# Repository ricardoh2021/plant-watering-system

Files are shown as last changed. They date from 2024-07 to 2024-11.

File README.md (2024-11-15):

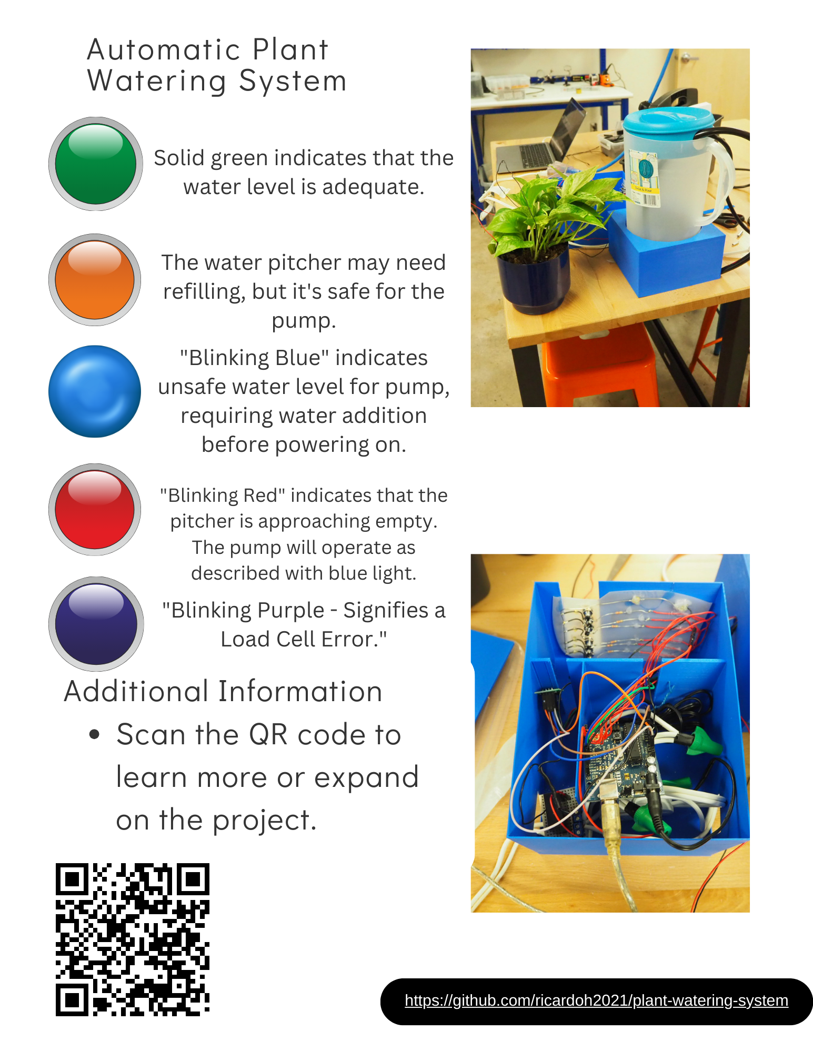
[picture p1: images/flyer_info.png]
System Flyer


# Water 1.1

**Author:** Ricardo Hernandez

## Table of Contents

1. [Description](#description)
2. [Changelog](#changelog)
3. [IDE Setup Instructions](#ide-setup-instructions)
4. [Advice for Beginners](#advice-for-beginners)
5. [Plant Watering System Documentation](#plant-watering-system-documentation)
   - [Overview](#overview)
   - [Components](#components)
   - [Pin Definitions](#pin-definitions)
   - [Arduino Wiring Schematic](#arduino-wiring-schematic)
   - [Configuration](#configuration)
   - [Functional Description](#functional-description)
     - [LED Indicators](#led-indicators)
     - [LED Blinks](#led-blinks)
     - [Error Handling](#error-handling)
   - [Functions](#functions)
     - [`setColor(int R, int G, int B)`](#setcolorint-r-int-g-int-b)
     - [`blinkLed(int R, int G, int B, unsigned long duration, unsigned long blinkInterval)`](#blinkledint-r-int-g-int-b-unsigned-long-duration-unsigned-long-blinkinterval)
     - [`blinkPurple()`](#blinkpurple)
     - [`blinkRed()`](#blinkred)
     - [`blinkBlue()`](#blinkblue)
     - [`resetLeds()`](#resetleds)
     - [`insertionSort(int* arr, int n)`](#insertionsortint-arr-int-n)
     - [`performMoistureReadings()`](#performmoisturereadings)
     - [`updateMoistureStatus()`](#updatemoisturestatus)
     - [`checkMoisture()`](#checkmoisture)
     - [`waterPlant()`](#waterplant)
     - [`checkLoadCellError(float weight)`](#checkloadcellerrorfloat-weight)
   - [Initialization](#initialization)
   - [Main Loop](#main-loop)
   - [3D Printed Encasings](#3d-printed-encasings)
     - [Encasing for Scale and Pitcher](#encasing-for-scale-and-pitcher)
     - [Encasing for Arduino and Wires](#encasing-for-arduino-and-wires)
   - [Design Process in TinkerCAD](#design-process-in-tinkercad)
   - [Printing with Innovation Creativity Lab](#printing-with-innovation-creativity-lab)
   - [3D Printed Model Files](#3d-printed-model-files)
   - [Known Issues and Troubleshooting](#known-issues-and-troubleshooting)
   - [Failsafe Values](#failsafe-values)
6. [General Tips](#general-tips)
7. [Future Modifications](#future-modifications)
8. [Upgrade Considerations](#upgrade-considerations)
   - [Hardware Upgrade Suggestions](#hardware-upgrade-suggestions)
   - [Possible Modifications for Indoor Plant Watering System](#possible-modifications-for-indoor-plant-watering-system)
9. [Nail Placement](#nail-placement)
10. [General TroubleSHooting](#general-troubleshooting)

## Description

Water 1.0 is an automated plant watering system that uses sensors to measure soil moisture and controls a pump via a relay to water the plant when needed. This project is inspired by the Botanicalls and Growduino concepts.

For information about the original project started by Leo Marte `09, visit: [Water 1.0 Project](http://cs.gettysburg.edu/~tneller/cs450/08fa/Physical_Computing/Plant_Watering.html)

## Changelog

- **2024-07-22:** (Ricardo Hernandez) Optimized and refactored code for better readability and performance. Updated comments.
- **2024-08-31:** (Ricardo Hernandez) Integrated Load Cell Scale, RGB LED, into the watering system.

## IDE Setup Instructions

(as of July 23, 2024 using v2.3.2)

1. Ensure you have the latest version of the Arduino IDE installed.
2. Select the correct board and port:
   - **Board:** Arduino Duemilanove or Diecimila
   - **Port:** Select the appropriate COM port
     - On Windows: Select the appropriate COM port (e.g., COM3, COM4, etc.)
     - On macOS: Select the appropriate port (e.g., /dev/tty.usbmodemxxxxx or /dev/cu.usbserial-xxxxx)
3. Select the correct processor:
   - **Processor:** ATmega168 (Due to the age of the Arduino)
4. Compile and upload the code to the Arduino board.

## Advice for Beginners

If you’re new to this and feeling overwhelmed, my advice is simple: just go for it! Don't be afraid to dive in and learn something new along the way. There are countless YouTube videos and tutorials on Arduino projects that can guide you. Break the problem down into smaller pieces and build from there. Start experimenting—it's the best way to learn.

This project is meant for you to expand on! Take advantage of all the tools Gettysburg College offers, like the Innovation and Creativity Lab. Don’t hesitate to ask whoever is in charge of the lab for help. Professor Neller is also a fantastic resource, so don’t be intimidated by all the wiring (my fault, haha) or if it seems complicated at first. Looks can be deceiving, but you can always start with a personal Arduino kit to get familiar with how things work. Take baby steps, and you’ll find yourself understanding more and more as you go. Enjoy your time at Gettysburg College and feel free to clone this branch and expand on it!

TL;DR

- Just dive in—learning by doing is the best approach.
- Use YouTube and tutorials to guide you through Arduino projects.
- Break the problem into smaller pieces and build from there.
- Leverage Gettysburg College’s Innovation and Creativity Lab.
- Don’t hesitate to ask for help; Professor Neller is a great resource.
- Start with a personal Arduino kit to get familiar with the basics.

Have fun!

## Plant Watering System Documentation

### Overview

This documentation describes the functionality and configuration of a plant watering system. The system uses a load cell to measure the weight of the water pitcher, moisture sensors to determine soil moisture, and an RGB LED for feedback. It also includes failsafe conditions to handle errors and abnormal situations.

### Components

- **Load Cell**: Measures the weight of the water pitcher.
- **HX711**: Amplifies and converts the load cell signal.
- **Moisture Sensors**: Measures soil moisture levels.
- **RGB LED**: Provides visual feedback about the system status.
- **Relay**: Controls the water pump.
- **EEPROM**: Stores the zero factor for the load cell.
- **Arduino**: Arduino Diecimila

### Pin Definitions

- **Load Cell DOUT Pin**: `A4`
- **Load Cell SCK Pin**: `A5`
- **Red LED Pin**: `10`
- **Green LED Pin**: `11`
- **Blue LED Pin**: `12`
- **Relay Pin**: `9`
- **Power Pin**: `8`
- **Moisture Probe Pin**: `0`
- **Status LEDs**: Pins `2-7`

### Arduino Wiring Schematic

Below is the wiring schematic for the plant watering system using Arduino.

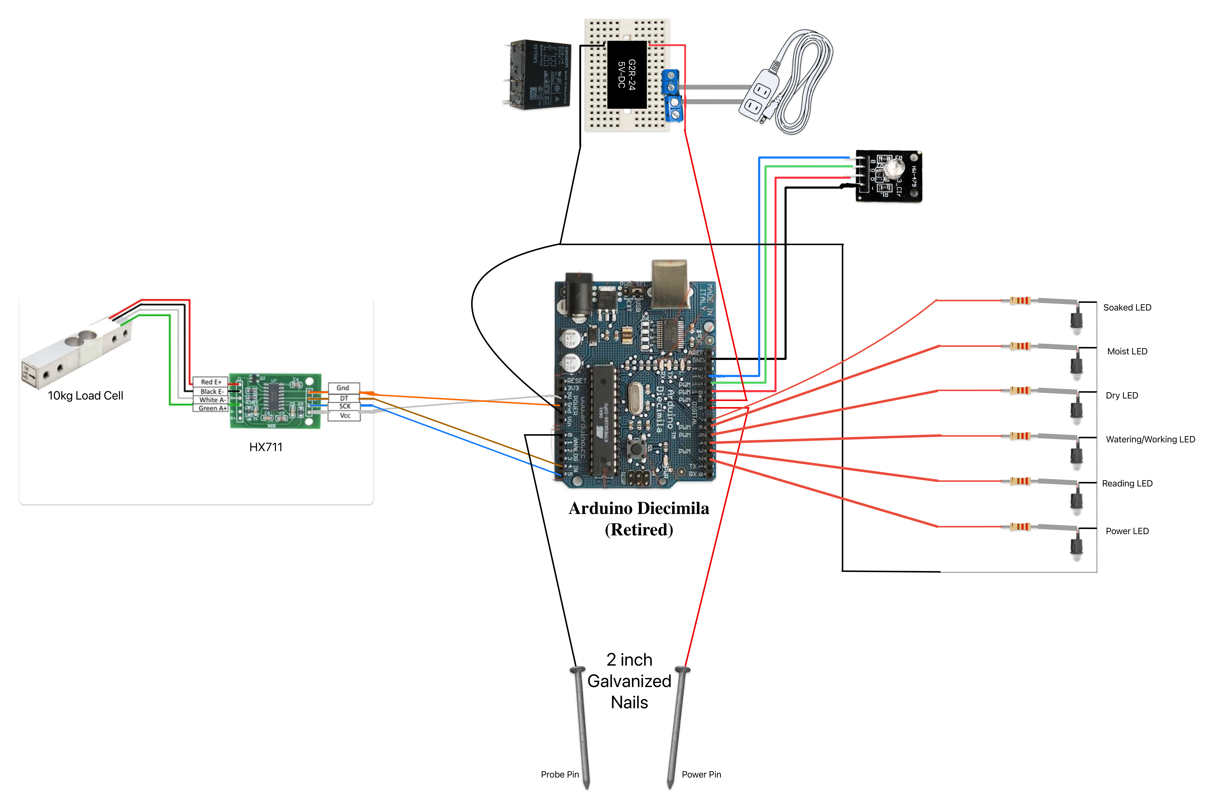
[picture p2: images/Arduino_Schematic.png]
Arduino Wiring Schematic


### Configuration

- **RGB LED Brightness Level**: `0.5`
- **Calibration Factor**: `-94500`
- **Weight Thresholds**:
  - **Empty Weight Threshold**: `1.65 lbs`
  - **Low Weight Threshold**: `3.00 lbs`
  - **Sufficient Weight Threshold**: `4.00 lbs`
- **Moisture Levels**:
  - **Dry**: `420`
  - **Moist**: `710`
  - **Soaked**: `1000`
- **Intervals**:
  - **Moisture Check Interval**: `10000 ms`
  - **Moisture Sample Interval**: `2000 ms`
  - **Water Interval**: `3000 ms`
  - **Failsafe Value**: `200`

### Functional Description

#### LED Indicators

- **Dry LED (Pin 5)**: Indicates that the soil is very dry.
- **Moist LED (Pin 6)**: Indicates that the soil is moist.
- **Soaked LED (Pin 7)**: Indicates that the soil is soaked.

#### LED Blinks

- **Purple Blink**: Indicates a load cell error.
- **Red Blink**: Indicates that the water level is too low.
- **Blue Blink**: Indicates a low water level warning.

#### Error Handling

- **Load Cell Error**: Detected if weight readings are outside a plausible range. The system blinks purple and sets `pumpEnabled` to `true`.
- **Low Water Level**: Detected if weight is below `EMPTY_WEIGHT_THRESHOLD` or `LOW_WEIGHT_THRESHOLD`. The system blinks red or blue, respectively, and sets `lowWaterLevel` to `true`.

### Functions

#### `setColor(int R, int G, int B)`

Sets the color of the RGB LED by adjusting the brightness of the red, green, and blue components.

#### `blinkLed(int R, int G, int B, unsigned long duration, unsigned long blinkInterval)`

Blinks the RGB LED with the specified color, duration, and interval.

#### `blinkPurple()`

Blinks the LED purple to indicate an error.

#### `blinkRed()`

Blinks the LED red to indicate a low water level.

#### `blinkBlue()`

Blinks the LED blue to indicate a low water level warning.

#### `resetLeds()`

Turns off all moisture status LEDs.

#### `insertionSort(int* arr, int n)`

Sorts an array of integers using insertion sort.

#### `performMoistureReadings()`

Averages moisture sensor readings over a defined interval and updates the average moisture level.

#### `updateMoistureStatus()`

Updates the status LEDs and triggers watering based on the average moisture level.

#### `checkMoisture()`

Determines if the plant needs watering based on moisture sensor readings.

#### `waterPlant()`

Controls the relay to water the plant if conditions are met.

#### `checkLoadCellError(float weight)`

Checks for errors in load cell readings and adjusts the system state accordingly.

### Initialization

The initialization routine sets up pin modes, initial states, and EEPROM values.

### Main Loop

The main loop continuously checks moisture levels, updates system status, and triggers watering actions based on the current conditions.

### 3D Printed Encasings

#### Encasing for Scale and Pitcher

A custom 3D printed case was designed to hold the scale and water pitcher securely.

#### Encasing for Arduino and Wires

A separate 3D printed case was created to keep the Arduino and wires organized.

### Printing with Innovation Creativity Lab

The encasings were printed using the facilities at the Innovation Creativity Lab at Gettysburg College.

### 3D Printed Model Files

Model files for the 3D printed encasings are available in the 3D Printed Model Files Folder

### Known Issues and Troubleshooting

- **Incorrect Load Cell Readings**: Verify wiring connections and solder joints.
- **Moisture Sensor Calibration**: Check soil and adjust thresholds as needed.

### Failsafe Values

- **Default Zero Factor**: `28974`
- **Empty Weight Threshold**: `1.65 lbs`
- **Low Weight Threshold**: `3.00 lbs`
- **Sufficient Weight Threshold**: `4.00 lbs`

## General Tips

1. Regularly check soldering joints for loose connections.
2. Ensure the water pitcher is correctly placed on the scale.
3. Clean the moisture sensors periodically to avoid false readings.
4. Use waterproofing measures for the electronics in case of accidental water spills.

## Future Modifications

### Upgrade Considerations

#### Hardware Upgrade Suggestions

- Upgrade to a more accurate load cell with a higher weight capacity.
- Add additional sensors, such as temperature or humidity sensors.
- Upgrade to more accurate soil sensors. Here is a [video tutorial](https://www.instructables.com/Arduino-Soil-Moisture-Sensor/) to help you out.
  - For even better readings, consider using a non-corrosive sensor, such as the one in this [tutorial](https://arduino-tutorials.net/tutorial/capacitive-soil-moisture-sensor-arduino). Here are some [Amazon Products](https://www.amazon.com/s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) that you could look into.
- Include a breadboard for better prototyping and cleaner wire management.
- Use a float switch instead of the load cell for accurate readings of the water level.
- Consider waterproofing the case that holds the water pitcher to prevent water damage to the scale.
- Replace the LED lights with a TFT LCD touchscreen that will display plant information via a GUI!

#### Possible Modifications for Indoor Plant Watering System

- Incorporate a Wi-Fi module to remotely monitor and control the system.
- Implement a mobile app for real-time notifications and control.

## Nail Placement

Place the nails at least 2-3 inches apart in the soil for more accurate moisture readings. Ensure they are inserted deep enough to measure the soil's moisture content effectively.

## General Troubleshooting

- Isolate the issue.
  - If issue related to Load Cell or LED, upload Load Cell specific code to debug.
  - If issue is related to Moisture Sensors, upload the original Water 1.0 file to isolate the issue to the Mositure Sensors.
- Check connections! Make sure everything is plugged in and there is nothing loose. Check Schematic to help you if needed.
- Ensure that the scale is placed in the middle, otherwise it will give innacurate readings.
- Ensure that nails are not placed close together as this can give innaccurate readings.
- Ensure the pump is connected via the mini breadboard wires and also through the extension cord.

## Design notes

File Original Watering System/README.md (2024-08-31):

# Project Description and Credits

**Original Author:** Leo Marte, Computer Science, Gettysburg College class of 2009.

## Project Description

This project combines concepts from two distinct projects: **Botanicalls** and **Growduino**. The primary objective is to integrate the knowledge from both sources to create an autonomous plant watering system. The system detects moisture levels in the plant and powers a water pump when the plant requires water, effectively allowing the plant to be watered without human intervention, assuming the reservoir is refilled regularly.

### Challenges and Calibration

One of the significant challenges was translating electrical readings from the plant into a meaningful state (dry, moist, or soaked). Extensive experimentation was conducted with two plants, Ralph and Lucy, to determine appropriate moisture readings:

- For Lucy, after being left without water for five days, the sensor reading was approximately 420 units, which was deemed the **DRY** state.
- Adding a full cup of water to Lucy resulted in a reading of about 1020 units, which was set as the **SOAKED** state.
- The midpoint between **DRY** and **SOAKED** was chosen as the **MOIST** state, calculated to be 710 units.

The Botanicalls project provided a useful tutorial on DIY sensors. Although the initial code and circuit were created without a relay, the wiring was prepared for future integration of a relay to complete the plant-watering system.

### Fault Tolerance

The project includes fault tolerance to avoid overwatering and flooding. If the moisture levels do not change after a watering action, the system will suspend operation, and the power light will blink to indicate a need for servicing.

### Controller Box Description

The controller box has two cables:

- **USB Cable:** Connects to a computer running Arduino software or a serial terminal for data communication.
- **Wall Plug:** Provides power to the water pump.

Inside the box:

- The extension cable is split to connect to the relay and the Arduino.
- The remaining extension cord with three outlets extends out of the box and connects to the plant probes.

The outlets are only live when the Arduino signals the relay to close and activate the water pump. The relay stays closed for approximately three seconds by default, ensuring the plant receives water without human intervention.

### Troubleshooting

This file is particularly useful for isolating just the watering system and troubleshooting the moisture sensors independently. It allows you to test and refine the moisture sensing functionality separately from the overall plant-watering system.

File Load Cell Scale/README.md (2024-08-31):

# `load_cell_rgb.ino` - README

## Overview

The `load_cell_rgb.ino` Arduino sketch interfaces with a 10kg load cell using the HX711 module and controls an RGB LED to indicate the water level in a pitcher.

**Author:** Ricardo Hernandez  
**Date:** August 2024

### Description

This sketch reads weight data from a 10kg load cell connected to the HX711 module. The load cell measures the weight of a water pitcher. Based on the weight, the RGB LED displays different colors to indicate the water level:

- **Red:** Empty or low water level
- **Yellow:** Sufficient water level
- **Green:** Full water pitcher

The code includes calibration and zero factor handling using EEPROM to ensure accurate weight measurements.

**Note:** This file is particularly useful if you want to isolate and troubleshoot issues related to the load cell and the RGB LED. It allows you to focus specifically on debugging these components without the complexity of the full system.

## Components

- **10kg Load Cell** with HX711 Amplifier
- **RGB LED**
- **Arduino Diecimila (ATmega168)**
- **Connecting Wires**

## Pin Definitions

- **Load Cell Pins:**
  - `LOADCELL_DOUT_PIN`: Analog pin A4 (DOUT of HX711)
  - `LOADCELL_SCK_PIN`: Analog pin A5 (SCK of HX711)
- **RGB LED Pins:**
  - `RED_PIN`: Digital pin 10
  - `GREEN_PIN`: Digital pin 11
  - `BLUE_PIN`: Digital pin 12

## Calibration

The code includes automatic calibration and zero factor handling:

1. **Initial Setup:**
   - The scale is tared (reset to zero).
   - The zero factor is stored in EEPROM if not already present.
2. **Calibration Factor:**
   - Adjust the `CALIBRATION_FACTOR` to match your scale setup.

## Thresholds

- **Empty Weight Threshold:** 1.50 lbs
- **Low Weight Threshold:** 3.50 lbs
- **Sufficient Weight Threshold:** 4.00 lbs

## LED Color Indications

- **Red:** Water pitcher is empty or low.
- **Yellow:** Water pitcher has sufficient weight.
- **Green:** Water pitcher is full.

## Functions

- `setColor(int R, int G, int B)`: Sets the color of the RGB LED.
- `blinkRed()`: Blinks the red LED to indicate an empty pitcher.

## Main Loop

The main loop:

1. Reads weight from the load cell.
2. Updates the RGB LED color based on weight thresholds.
3. Allows for serial input to reset the zero factor by sending 'z' or 'Z'.

## Troubleshooting

### Common Issues

1. **Wiring Problems:**
   - Ensure all connections are secure and correctly matched with the pins.
2. **Soldering Quality:**

   - **Note:** My soldering skills are beginner level at best. If you are experienced with soldering, consider fixing any wiring issues before changing the code, as most problems are often due to poor connections.

3. **Load Cell Issues:**

   - If you encounter load cell issues, upload the `load_cell_rgb.ino` file to the Arduino. This file focuses on debugging the load cell separately from the main code.

4. **EEPROM Issues:**
   - Check EEPROM functionality if there are problems with storing or retrieving the zero factor.

## Notes

- Adjust the `CALIBRATION_FACTOR` to match your specific scale setup for accurate readings.
- Regularly check and maintain the system to ensure reliable operation.

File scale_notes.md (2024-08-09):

# Work Log: Setting Up 10kg Load Cell for Plant Watering System

## Date: August 8, 2024

## Equipment Used:

- **10kg Load Cell** (Bought from [Amazon](https://www.amazon.com/Geekstory-Converter-Breakout-Electronic-Raspberry/dp/B0D293F1CW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))
- **HX711 Load Cell Amplifier**
- **Arduino Diecimila (ATmega168)**
- **Soldering Iron and Solder**
- **Female Dupont Connectors**
- **Multimeter** (for testing resistance)
- **Wires and Pins** (for extending connections)

## Work Done:

- Followed this video to ensure setup was smooth as possible. [Tutorial](https://www.youtube.com/watch?v=sxzoAGf1kOo&t=356s)
- Set up the 10kg load cell with the HX711 Load Cell Amplifier connected to Arduino Diecimila (ATmega168).
- Soldered pins onto the HX711 to extend the wires for better connection.
- Tested the resistance between the wires to ensure that the sensors were being read correctly.
  - Had to troubleshoot readings that were extremely off and not detecting any resistance.
  - Narrowed it down to the wiring not connecting well between the wire and the female Dupont connector.
  - Decided to solder the wires together for a better connection.
- Played around with the calibration number to correct the scale readings.
- Conducted troubleshooting for an issue with the water pump, which was not receiving power. Identified that two cables inside the enclosure were loose. Specifically, Pin 9 was not connected to the A1 Coil pin, and the black GND pin was not connected to the A2 Coil pin. After reconnecting the cables appropriately, verified functionality by testing the system on several dry plants around the house. The water pump performed as expected, confirming that the issue was resolved.

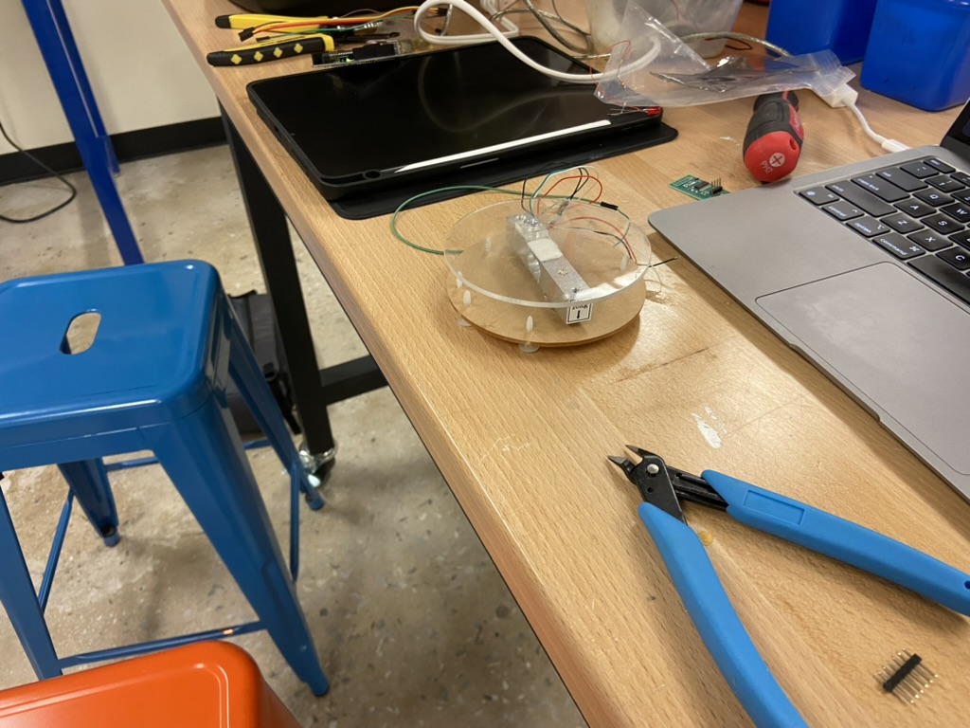
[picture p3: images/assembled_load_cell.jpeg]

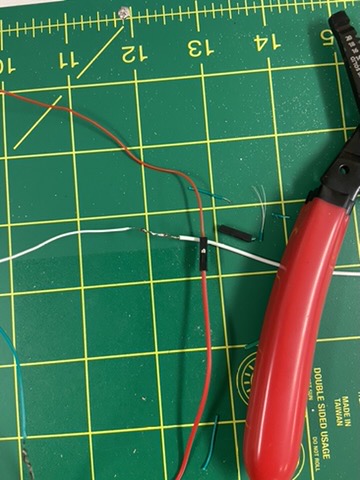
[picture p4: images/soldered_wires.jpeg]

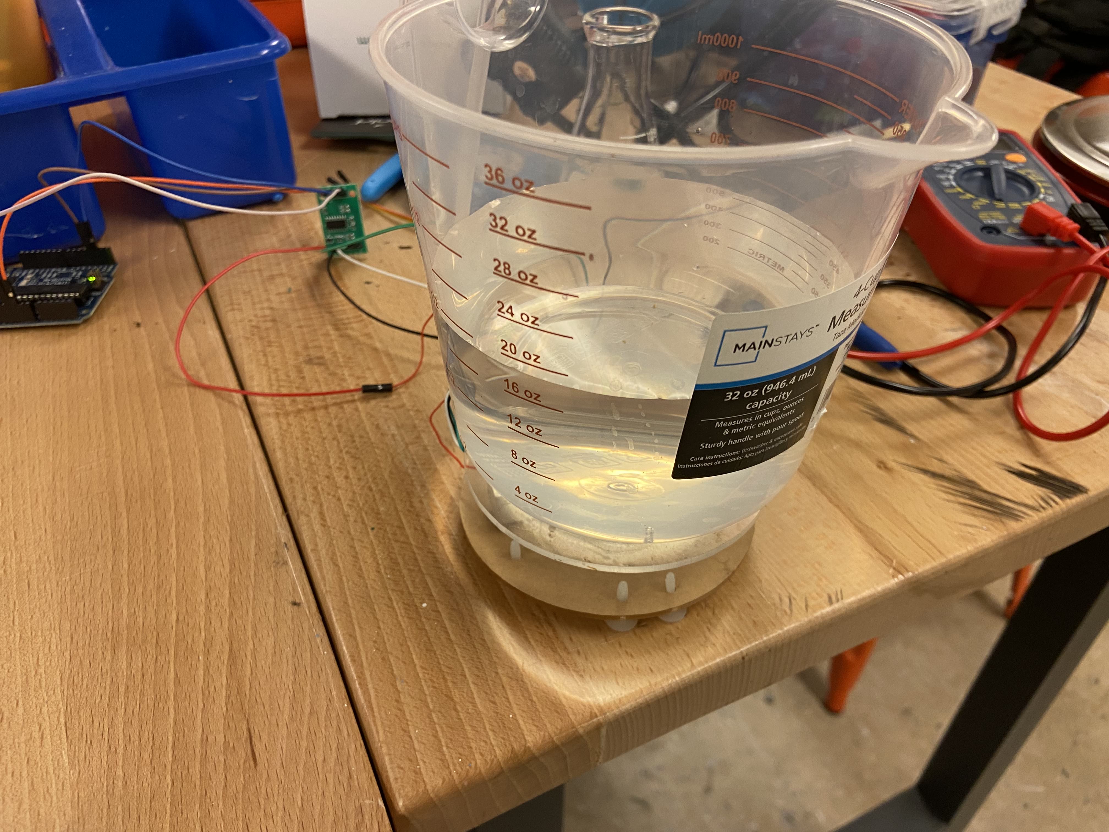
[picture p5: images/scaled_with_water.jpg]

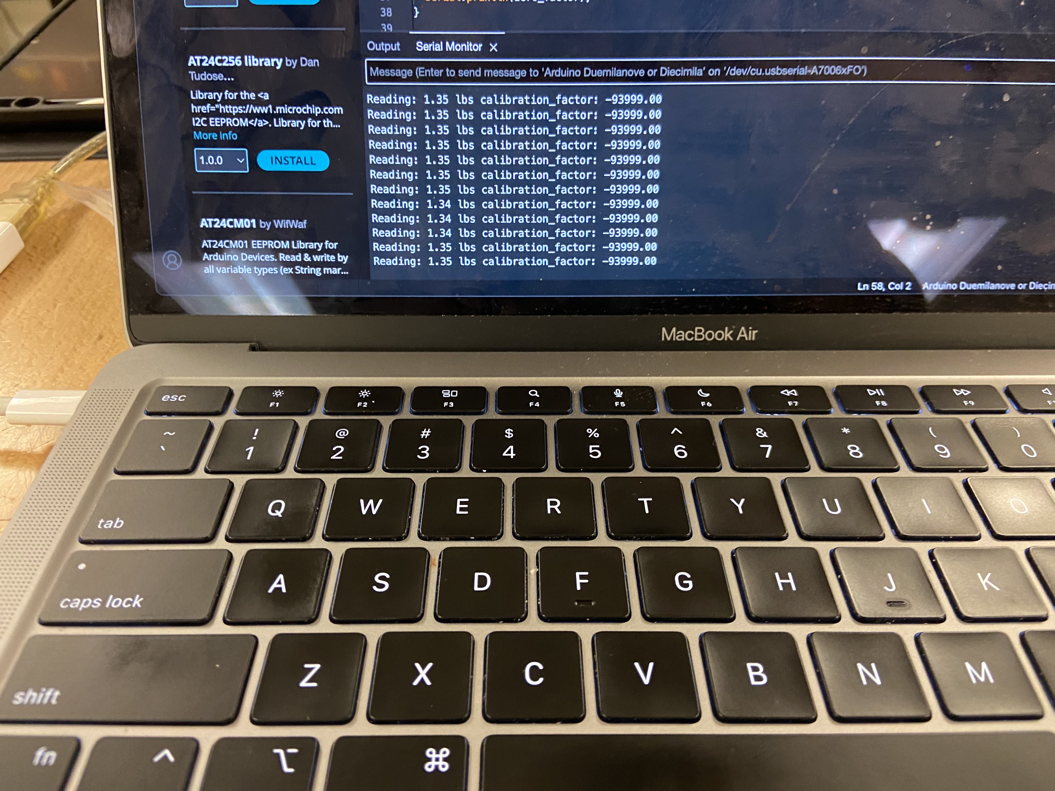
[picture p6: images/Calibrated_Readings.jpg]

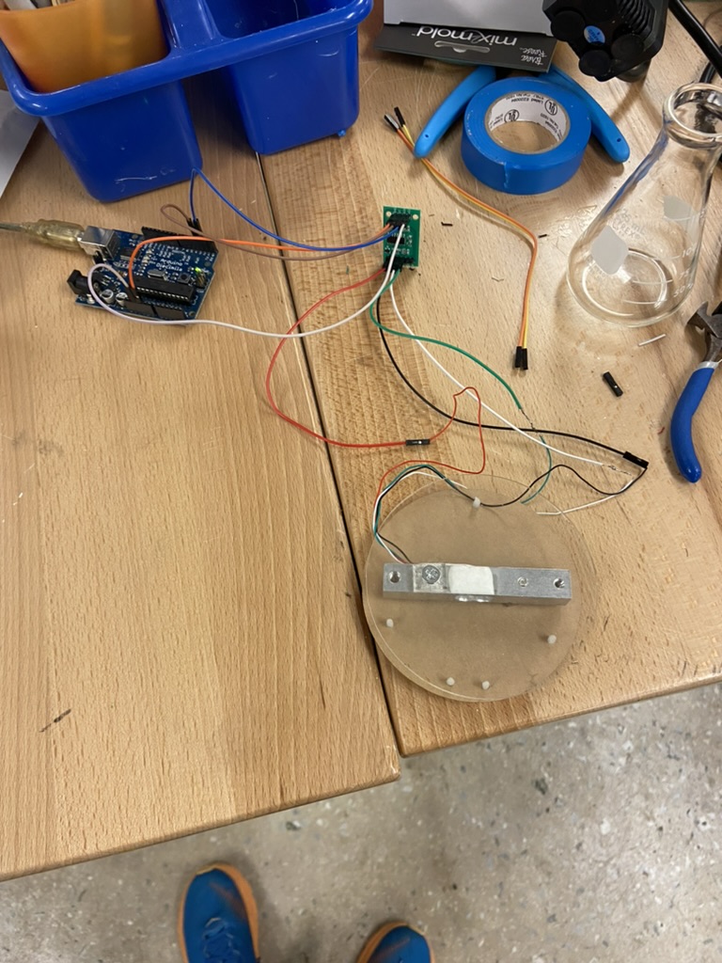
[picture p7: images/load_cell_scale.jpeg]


## Following Steps:

- Create a 3D Printed Case: Design and print a case to hold the scale in place, including a section to securely hold the water pitcher.
- Add LED Indicators: Integrate LED lights that will be triggered when the water level in the pitcher is too low.
- Code Integration: Merge this code with the existing water.ino file and integrate the wiring with the current Arduino setup to fully automate the plant watering system.
- Create diagrams of the wiring for future students to use. I have to make sure that I write good documentation.

## Code:

```cpp
#include "HX711.h"
#include <EEPROM.h> // Include EEPROM library for storing the zero factor

// Pin definitions for the HX711 module
#define LOADCELL_DOUT_PIN  3  // Pin connected to DOUT of HX711
#define LOADCELL_SCK_PIN   2  // Pin connected to SCK of HX711

// EEPROM memory address for storing the zero factor
#define EEPROM_ADDRESS 0

HX711 scale;  // Create an instance of the HX711 class

// Calibration factor for scaling the raw data to weight units
float calibration_factor = -93999; // Adjust this value to match your scale setup

/**
 * @brief Arduino setup function.
 *
 * Initializes serial communication, sets up the HX711 load cell,
 * and loads the zero factor from EEPROM. If no valid zero factor is found,
 * the scale is tared, and the zero factor is stored in EEPROM.
 */
void setup() {
  Serial.begin(9600);  // Initialize serial communication at 9600 baud rate
  Serial.println("HX711 calibration sketch");
  Serial.println("Remove all weight from scale");
  Serial.println("After readings begin, place known weight on scale");

  scale.begin(LOADCELL_DOUT_PIN, LOADCELL_SCK_PIN);  // Initialize the HX711 module
  scale.set_scale();  // Set the scale to the default calibration factor

  // Load zero factor from EEPROM
  long zero_factor;
  EEPROM.get(EEPROM_ADDRESS, zero_factor);  // Retrieve stored zero factor from EEPROM
  if (zero_factor == 0xFFFFFFFF) {  // Check if no valid zero factor is found in EEPROM
    Serial.println("No zero factor found in EEPROM. Please tare the scale manually.");
    scale.tare();  // Manually tare the scale (reset to 0)
    zero_factor = scale.read_average();  // Get a baseline reading for the zero factor
    EEPROM.put(EEPROM_ADDRESS, zero_factor);  // Save the new zero factor to EEPROM
  } else {
    scale.set_offset(zero_factor);  // Apply the stored zero factor to the scale
    Serial.println("Zero factor loaded from EEPROM.");
  }

  Serial.print("Zero factor: ");  // Display the loaded or newly set zero factor
  Serial.println(zero_factor);
}

/**
 * @brief Arduino main loop function.
 *
 * Continuously reads the weight from the scale, applies the calibration factor,
 * and prints the results to the serial monitor. The calibration factor can be adjusted
 * through the serial interface.
 */
void loop() {
  scale.set_scale(calibration_factor);  // Apply the current calibration factor

  // Print the weight reading and the current calibration factor to the serial monitor
  Serial.print("Reading: ");
  Serial.print(scale.get_units(), 2);  // Display the weight with 2 decimal places
  Serial.print(" lbs");  // Display the units (lbs by default)
  Serial.print(" calibration_factor: ");
  Serial.print(calibration_factor);
  Serial.println();

  delay(1000);  // Delay for 1 second to allow stable readings
}
```

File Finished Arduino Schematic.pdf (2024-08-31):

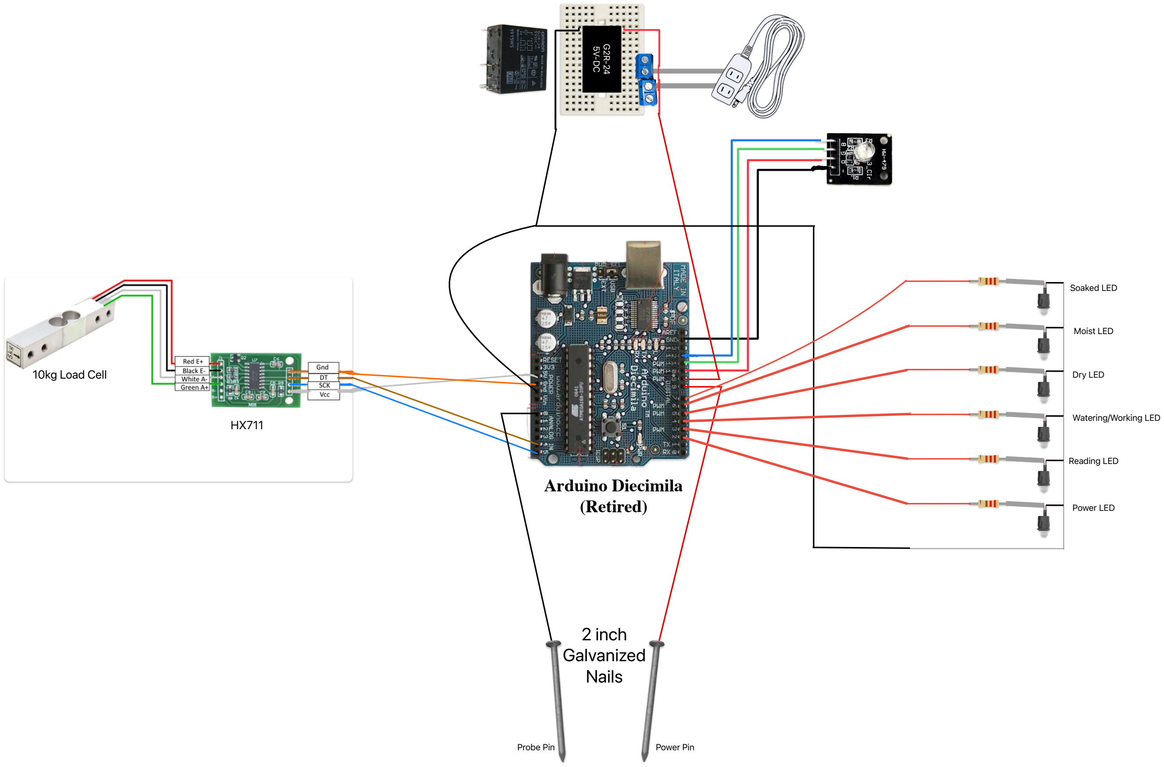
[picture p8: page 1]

5V-DC

G2R-24

Power LED

Reading LED

Watering/Working LED

Dry LED

Moist LED

Soaked LED

# 2 inch Galvanized Nails

Probe Pin | Power Pin

# Arduino Diecimila (Retired)

## 10kg Load Cell

HX711

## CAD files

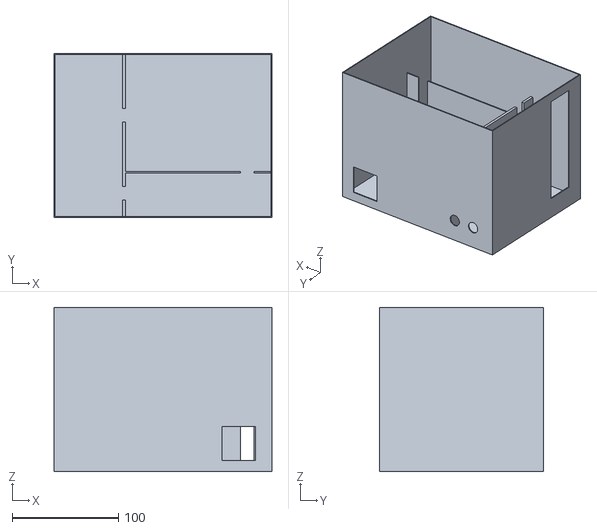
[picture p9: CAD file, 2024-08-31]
3D Printed Model Files/Electronics_case.stl
205.2 x 154.4 x 154.4

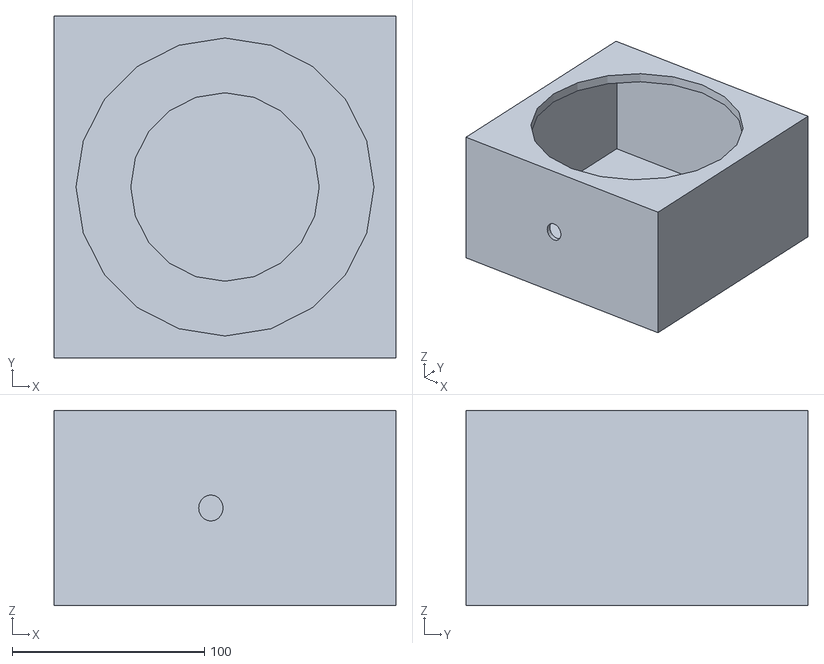
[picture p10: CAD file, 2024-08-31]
3D Printed Model Files/Automatic_Watering_System.stl
177.8 x 177.8 x 101.6

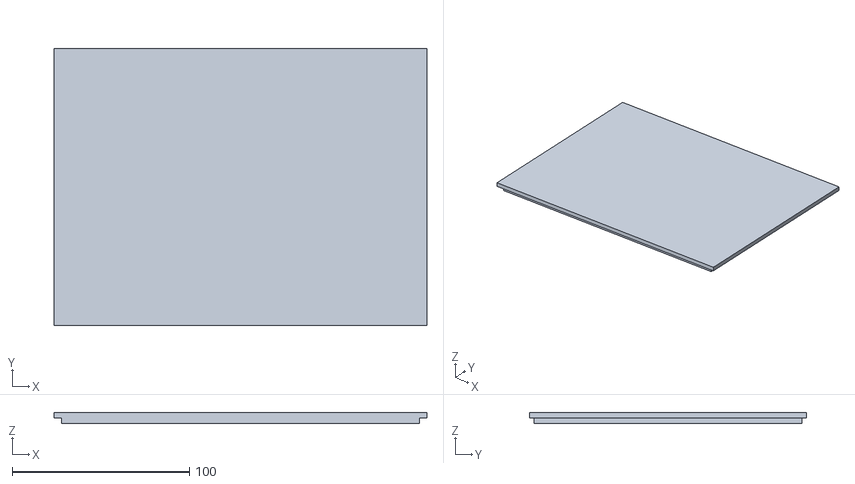
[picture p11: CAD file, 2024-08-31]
3D Printed Model Files/Electronics_case_lid.stl
210.2 x 156.2 x 6.48

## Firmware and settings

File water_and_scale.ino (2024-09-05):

#include "HX711.h"
#include <EEPROM.h>

// Pin definitions for the HX711 module
const int LOADCELL_DOUT_PIN = A4;  // Pin connected to DOUT of HX711 (Analog pin A4)
const int LOADCELL_SCK_PIN = A5;   // Pin connected to SCK of HX711 (Analog pin A5)

// Pin definitions for the RGB LED
const int RED_PIN = 10;    // Pin connected to the red leg of the LED
const int GREEN_PIN = 11;  // Pin connected to the green leg of the LED
const int BLUE_PIN = 12;   // Pin connected to the blue leg of the LED

// EEPROM memory address for storing the zero factor
const int EEPROM_ADDRESS = 0;

// Weight thresholds (in lbs)
const float EMPTY_WEIGHT_THRESHOLD = 1.65; // Under this is empty
const float LOW_WEIGHT_THRESHOLD = 3.00;
const float SUFFICIENT_WEIGHT_THRESHOLD = 4.00;

// Calibration factor for scaling the raw data to weight units
const float CALIBRATION_FACTOR = -94500; // Adjust this value to match your scale setup

HX711 scale;  // Create an instance of the HX711 class

/* DEFINE YOUR BOTANICAL PREFERENCES */

#define DRY 420
#define MOIST 710
#define SOAKED 1000

/* DEFINE CONSTANTS */

#define MOIST_CHECK_INTERVAL 10000   // milliseconds between checks
#define MOIST_SAMPLE_INTERVAL 2000   // milliseconds over which to average reading samples
#define WATER_INTERVAL 3000          // milliseconds to allow for water to flow
#define MOIST_SAMPLES 10             // # of samples to average when reading moisture
#define FAILSAFE_VALUE 200           // minimum difference in moisture indicating watering

/* PROGRAM VARIABLES AND BOARD PINS */

// LEDs
#define onLed 2
#define readLed 3
#define workLed 4
#define dryLed 5
#define moistLed 6
#define soakedLed 7

// probes
#define powerPin 8
#define relayPin 9
#define probePin 0

int moistValues[MOIST_SAMPLES];
unsigned long lastMoistTime = 0;
unsigned long lastWaterTime = 0;
int lastMoistAvg = 0;
int oldlastMoistAvg = 0;
boolean needServicing = false;
boolean wateredLast = false;
boolean pumpEnabled = true;
boolean lowWaterLevel = false;  // Global variable to track low water level status

const long DEFAULT_ZERO_FACTOR = 28974;  // Default zero factor in case EEPROM read fails

boolean loadCellError = false;  // Global variable to track load cell errors

// Define a constant for the brightness level (percentage from 0 to 100)
const float BRIGHTNESS_LEVEL = 0.5; // 50% brightness


/* HELPER METHODS */

/**
 * @brief Sets the color of the RGB LED by adjusting the brightness of the red, green, and blue components.
 * 
 * This function takes in RGB values and scales them according to the specified brightness level.
 * The brightness level can be modified via the BRIGHTNESS_LEVEL constant.
 * 
 * @param R The intensity of the red component (0 to 255).
 * @param G The intensity of the green component (0 to 255).
 * @param B The intensity of the blue component (0 to 255).
 * 
 * The function scales each RGB value based on the BRIGHTNESS_LEVEL constant before writing them to the
 * respective RGB pins using analogWrite.
 */
void setColor(int R, int G, int B) {
    analogWrite(RED_PIN, R * BRIGHTNESS_LEVEL);
    analogWrite(GREEN_PIN, G * BRIGHTNESS_LEVEL);
    analogWrite(BLUE_PIN, B * BRIGHTNESS_LEVEL);
}

/**
 * @brief Function to blink an LED with customizable color and duration.
 * 
 * @param R Red component (0-255).
 * @param G Green component (0-255).
 * @param B Blue component (0-255).
 * @param duration Total duration for blinking (milliseconds).
 * @param blinkInterval Interval between blinks (milliseconds).
 */
void blinkLed(int R, int G, int B, unsigned long duration, unsigned long blinkInterval) {
  unsigned long startTime = millis();
  while (millis() - startTime < duration) {
    setColor(R, G, B);
    delay(blinkInterval);
    setColor(0, 0, 0); // Turn off the LED
    delay(blinkInterval);
  }
}

/**
 * @brief Blink the RGB LED in purple color.
 * 
 * The LED blinks purple for a duration of 9000 milliseconds with a 500 milliseconds interval.
 */
void blinkPurple() {
  blinkLed(128, 0, 128, 9000, 500);
}

/**
 * @brief Blink the RGB LED in red color.
 * 
 * The LED blinks red for a duration of 9000 milliseconds with a 500 milliseconds interval.
 */
void blinkRed() {
  blinkLed(255, 0, 0, 9000, 500);
}

/**
 * @brief Blink the RGB LED in blue color.
 * 
 * The LED blinks blue for a duration of 9000 milliseconds with a 500 milliseconds interval.
 */
void blinkBlue() {
  blinkLed(0, 0, 255, 9000, 500);
}

/**
 * @brief Reset the state of the moisture status LEDs.
 * 
 * This function turns off all moisture status LEDs (dry, moist, soaked).
 */
void resetLeds() {
  digitalWrite(dryLed, LOW);
  digitalWrite(moistLed, LOW);
  digitalWrite(soakedLed, LOW);
}

/**
 * @brief Sort an array of integers using the insertion sort algorithm.
 * 
 * @param arr Pointer to the array to be sorted.
 * @param n Number of elements in the array.
 */
void insertionSort(int* arr, int n) {
  for (int i = 1; i < n; i++) {
    int key = arr[i];
    int j = i - 1;

    while (j >= 0 && arr[j] > key) {
      arr[j + 1] = arr[j];
      j = j - 1;
    }
    arr[j + 1] = key;
  }
}

/**
 * @brief Perform moisture readings by averaging multiple samples.
 * 
 * Reads moisture sensor values over a defined interval, sorts the readings, and updates
 * the average moisture level.
 */
void performMoistureReadings() {
  for (int i = 0; i < MOIST_SAMPLES + 1; i++) {
    digitalWrite(powerPin, HIGH);
    int val = analogRead(probePin);
    digitalWrite(powerPin, LOW);

    if (i != 0) {
      moistValues[i - 1] = val;
      lastMoistTime = millis();
    }

    delay(MOIST_SAMPLE_INTERVAL);
  }

  insertionSort(moistValues, MOIST_SAMPLES);
  oldlastMoistAvg = lastMoistAvg;
  lastMoistAvg = moistValues[MOIST_SAMPLES / 2];
}

/**
 * @brief Update the moisture status and control the watering process.
 * 
 * Updates the status LEDs based on the average moisture level and triggers the watering
 * process if needed.
 */
void updateMoistureStatus() {
  resetLeds();
  if (lastMoistAvg <= DRY) {
    Serial.println(" status: VERY DRY - watering plant");
    digitalWrite(dryLed, HIGH);
    waterPlant();
  } else if (lastMoistAvg < MOIST) {
    Serial.println(" status: DRY - watering plant");
    digitalWrite(dryLed, HIGH);
    waterPlant();
  } else if (lastMoistAvg < SOAKED) {
    Serial.println(" status: MOIST - plant is just fine");
    digitalWrite(moistLed, HIGH);
  } else {
    Serial.println(" status: SOAKED - don't water plant!");
    digitalWrite(soakedLed, HIGH);
  }
}

/**
 * @brief Perform a moisture check and update the plant watering status.
 * 
 * Reads the moisture sensor values, prints the average moisture level, and updates
 * the moisture status.
 */
void checkMoisture() {
  digitalWrite(readLed, HIGH);
  performMoistureReadings();
  Serial.print("median read: ");
  Serial.print(lastMoistAvg);
  Serial.print(" | ");
  updateMoistureStatus();
  digitalWrite(readLed, LOW);
}

/**
 * @brief Water the plant by activating the relay to control the pump.
 * 
 * If the moisture readings are not within the acceptable range or if the watering fails,
 * the system will enter a service mode. The pump will be activated to water the plant
 * for a defined interval.
 */
void waterPlant() {
  if(!pumpEnabled){
    return;
  }

  // Test for failsafe condition
  int diffMoist = lastMoistAvg - oldlastMoistAvg;

  if( wateredLast && diffMoist <= FAILSAFE_VALUE ){
    needServicing = true;
    Serial.println("");
    Serial.println("water 1.0 is suspending execution...");
    Serial.println("EQUIPMENT NEEDS SERVICING!");
    resetLeds();
    digitalWrite(readLed, LOW);
    while(true){
      // If sensor has an issue, flash onLed
      digitalWrite(onLed, LOW); 
      delay(1000);      
      digitalWrite(onLed, HIGH);
      delay(1000);  
    }
  }
  else{
    // Output info to serial
    Serial.print("watering started at: ");
    Serial.print(millis());
    digitalWrite(workLed, HIGH); // Light on working LED

    // Open relay, delay, and close
    digitalWrite(relayPin, HIGH);
    delay(WATER_INTERVAL);
    digitalWrite(relayPin, LOW);  // COMMENTED ONLY WHEN THERE IS NO RELAY ATTACHED

    // Output info to serial
    digitalWrite(workLed, LOW);     
    Serial.print(", it lasted: ");
    Serial.print(WATER_INTERVAL);
    Serial.print(" seconds");
    Serial.println("");
    
    wateredLast = true;
  }
}

/**
 * @brief Initialize the Arduino board and set up the HX711 scale.
 * 
 * Configures the pin modes for LEDs, relay, and other components. Initializes serial
 * communication, starts the HX711 scale, and loads the zero factor from EEPROM.
 * Sets the calibration factor and offset for the scale.
 */
void setup() {
  pinMode(onLed, OUTPUT);
  pinMode(readLed, OUTPUT);
  pinMode(workLed, OUTPUT);
  pinMode(dryLed, OUTPUT);
  pinMode(moistLed, OUTPUT);
  pinMode(powerPin, OUTPUT);
  pinMode(relayPin, OUTPUT);

  digitalWrite(onLed, HIGH);
  Serial.begin(9600);
  Serial.println("water 1.0 up and running...");
  Serial.println("");

  scale.begin(LOADCELL_DOUT_PIN, LOADCELL_SCK_PIN);  // Initialize the HX711 module
  scale.set_scale();  // Set the scale to the default calibration factor

  // Load zero factor from EEPROM
  long zero_factor;
  EEPROM.get(EEPROM_ADDRESS, zero_factor);
  
  if (zero_factor == 0xFFFFFFFF || isnan(zero_factor) || zero_factor == 0) {
    Serial.println("EEPROM read failed or data is invalid. Using default zero factor.");
    zero_factor = DEFAULT_ZERO_FACTOR;  // Use default zero factor
    EEPROM.put(EEPROM_ADDRESS, zero_factor);  // Attempt to write default value back to EEPROM
  }
  
  scale.set_offset(zero_factor);  // Apply the zero factor

  // Set the RGB pins as output
  pinMode(RED_PIN, OUTPUT);
  pinMode(GREEN_PIN, OUTPUT);
  pinMode(BLUE_PIN, OUTPUT);
}

/**
 * @brief Check for load cell errors by verifying if the weight readings are within a plausible range.
 * 
 * Evaluates weight readings for stability and plausibility over a defined interval. If the readings
 * consistently fall outside the plausible range, an error is flagged.
 * 
 * @param weight Current weight reading from the scale.
 * @return true if a load cell error is detected; otherwise, false.
 */
bool checkLoadCellError(float weight) {
  // Define plausible weight range (adjust as needed)
  const float MIN_PLAUSIBLE_WEIGHT = -0.02;  // Minimum plausible weight
  const float MAX_PLAUSIBLE_WEIGHT = 10.0;   // Maximum plausible weight

  // Example stability check: verify if weight readings are consistently out of bounds
  static float prevWeight = 0;
  static unsigned long lastCheckTime = 0;
  const unsigned long CHECK_INTERVAL = 5000;  // Check interval in milliseconds
  const int STABILITY_COUNT = 10;  // Number of consecutive out-of-bound readings for error

  if (millis() - lastCheckTime > CHECK_INTERVAL) {
    lastCheckTime = millis();
    prevWeight = weight;  // Update previous weight reading
    return false;  // No error detected yet
  }

  static int outOfBoundCount = 0;

  if (weight < MIN_PLAUSIBLE_WEIGHT || weight > MAX_PLAUSIBLE_WEIGHT) {
    outOfBoundCount++;
    if (outOfBoundCount >= STABILITY_COUNT) {
      loadCellError = true;
      return true;  // Error detected
    }
  } else {
    outOfBoundCount = 0;  // Reset count if within bounds
  }

  loadCellError = false;
  return false;  // No error detected
}

/**
 * @brief Main loop of the Arduino program that performs regular tasks.
 * 
 * Continuously reads the weight from the HX711 scale, checks for load cell errors, and updates
 * the status of the plant watering system based on the weight and moisture readings. 
 * Includes a delay between iterations.
 */
void loop() {
  scale.set_scale(CALIBRATION_FACTOR);  // Apply the current calibration factor

  float weight = scale.get_units();  // Get the weight from the scale
  Serial.print("Weight is: ");
  Serial.print(weight);
  Serial.print(" lbs.");
  Serial.println();

  // Check for load cell errors
  if (checkLoadCellError(weight)) {
    Serial.println("Load cell error detected. Pump will be enabled regardless of water level.");
    blinkPurple(); // Blink purple to indicate error

    // Default mode: Enable pump regardless of water level
    pumpEnabled = true;
    lowWaterLevel = false;  // Clear the low water level flag in error state
    setColor(255, 0, 0);    // Optional: Indicate error with red LED
  } else {
    // Set LED color based on weight conditions and check water level
    if (weight < EMPTY_WEIGHT_THRESHOLD) {
      blinkRed();
      lowWaterLevel = true;  // Set the flag indicating low water level
      Serial.println("Water level too low! May harm pump.");
      pumpEnabled = false;
    } else if (weight < LOW_WEIGHT_THRESHOLD) {
      blinkBlue();
      lowWaterLevel = true;  // Set the flag indicating low water level
      Serial.println("Water level too low! Pump deactivated.");
    } else if (weight < SUFFICIENT_WEIGHT_THRESHOLD) {
      setColor(255, 255, 0);  // Yellow
      lowWaterLevel = false;  // Water level is sufficient, clear the flag
      pumpEnabled = true;
    } else {
      setColor(0, 255, 0);  // Green
      lowWaterLevel = false;  // Water level is sufficient, clear the flag
      pumpEnabled = true;
    }
  }

  // If water level is too low, load cell error detected, or pump failure detected, skip the moisture check
  if (lowWaterLevel || loadCellError) {
    Serial.println("Issues have occurred. Check Water Level. Otherwise, issue with Load Cell Scale.");
  }

  checkMoisture();

  Serial.print("delaying for ");
  Serial.print(MOIST_CHECK_INTERVAL / 1000);
  Serial.println(" seconds");
  Serial.println("");

  delay(MOIST_CHECK_INTERVAL);
}

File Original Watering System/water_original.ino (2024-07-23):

/*
 * Application: Water 1.0
 * Author: Leo Marte
 *
 * Sets up a system to water a plant, by using sensors to probe water moisture
 * and opening a pump (via a relay) to water the plant when needed. Combination
 * of Botanicalls and Growduino project concepts.
 *
 * http://cs.gettysburg.edu/~martle02/cs450/
 */

/* DEFINE YOUR BOTANICAL PREFERENCES */

//the botanicalls project defines by default
//the following threshold for your plant:
//#define MOIST 425             // minimum level of satisfactory moisture
//#define DRY 300               // maximum level of tolerable dryness      
//#define SOAKED 575            // minimum desired level after watering
//#define WATERING_CRITERIA 125 // minimum change in value that indicates watering

//I used the previous thresholds as a starting point
//to determine new ones for my pathos plant. below are the results:
#define DRY 420               // after not being watered for ~5 days
#define MOIST 710             // midpoint between DRY and SOAKED
#define SOAKED 1000           // least desired level after watering

//in order to figure out the bottom-line, or the DRY value, I left the pathos
//without water for about 5 days until the surface was completely dry, and the
//leaves started to get yellow (i know its cruel). At that point the reading
//was 420 on the analog input. I then poured a cup of water on it, and the
//reading value went up to about a 1000. I called that value my SOAKED value
//since I wouldn't want my plant to be more watered than that. Finally,
//I considered MOIST to be the midpoint between being too dry and soaked.
//Below is an example of my rationale:

//variation:
//1 cup of water -> 1000 (sensor reading) @ 7.30pm on 12/9/2008
//criteria of cup of water is: ~600 (reading increases by that amount)
//  if 1000 is SOAKED, then the midpoint between 420 and 1000: 710 is MOIST

/* DEFINE CONSTANTS */

//define here how often you would like things to happen, from moisture check
//frequency, to what do you want it to be the interval between reads to average,
//to how long to keep the water running. also select how many total samples you
//would like to collect to determine moisture levels every time the system checks

#define MOIST_CHECK_INTERVAL 10000   // milliseconds (1 minutes) in between checks
//#define MOIST_CHECK_INTERVAL 3600000 // milliseconds (1 hour) in between checks
#define MOIST_SAMPLE_INTERVAL 2000   // milliseconds over which to average reading samples
//#define MOIST_SAMPLE_INTERVAL 5000 // milliseconds over which to average reading samples

#define WATER_INTERVAL 3000          // milliseconds to allow for water to flow
// this value will change according to the kind of pump
// that you will use. some pumps will need more time
// to get  the water to the plant than the default 3 seconds.

#define MOIST_SAMPLES 10             // # of samples to average when reading moisture
#define FAILSAFE_VALUE 200           // minimum difference in moisture that indicates watering has happened

/* PROGRAM VARIABLES AND BOARD PINS */

//LEDs               //light up when:
#define onLed 2      //device is on
#define readLed 3    //device is reading
#define workLed 4    //device is watering
#define dryLed 5     //plant is anywhere below MOIST
#define moistLed 6   //plant is equal or higher than MOIST and less than SOAKED
#define soakedLed 7  //plant is equal or higher than SOAKED

//probes
#define powerPin 8 //sends current to plant
#define relayPin 9 //send current to activate relay
#define probePin 0 //analog 0: collects current from plant

int moistValues[MOIST_SAMPLES];  // array to store readings to average
unsigned long lastMoistTime=0;   // storage for millis of the most recent moisture reading
unsigned long lastWaterTime=0;   // storage for millis of the most recent watering reading
int lastMoistAvg=0;              // storage for moisture average of the most recent moisture reading
int oldlastMoistAvg=0;           // temp var for failsafe test
boolean needServicing = false;   // set if there is a faulty probe
boolean wateredLast = false;
/* HELPER METHODS */

void resetLeds(){
  //turn off all plant status leds
  digitalWrite(dryLed,     LOW);
  digitalWrite(moistLed,   LOW);
  digitalWrite(soakedLed,  LOW);
}

void selectionSort(){
  //sorts moistValues array using selection sort

  int indexOfMin;  //vars
  int pass;        //-
  int j;           //-

  //perform selection sort
  for ( pass = 0; pass < MOIST_SAMPLES - 1; pass++ ) { 
    indexOfMin = pass; 

    for ( j = pass + 1; j < MOIST_SAMPLES; j++ ) 
      if ( moistValues[j] < moistValues[pass] ) 
        indexOfMin = j; 

    int temp; 
    temp = moistValues[pass]; 
    moistValues[pass] = moistValues[indexOfMin]; 
    moistValues[indexOfMin] = temp; 
  }
 
  Serial.print("sorted readings: ");
  for(int i=0; i<MOIST_SAMPLES; i++){
    Serial.print(moistValues[i]);
    Serial.print(" ");
  }
  Serial.println(""); 
}
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

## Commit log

2024-08-09 Updated notes to include troubleshooting of pump
2024-08-13 Updated water to include load cell with LED
2024-08-15 scale update with LED
2024-08-21 Added check for pump when water low
2024-08-31 Arduino Schematic Added
2024-08-31 3D files added
    [Automatic_Watering_System.stl, Electronics_case.stl, Electronics_case_lid.stl]
2024-08-31 3D printed notes
